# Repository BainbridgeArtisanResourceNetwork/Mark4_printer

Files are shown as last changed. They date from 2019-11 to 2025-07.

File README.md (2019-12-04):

# Mark4_printer
Mark4 is the large-format 3D printer the ETA studio at BARN is building as a DIY community project.

## Specifications

- Motion stage: CoreXY
- Build volume: X=350mm, Y=350mm, Z>=400mm
- Controller: Duet 2 WiFi
- Extruder/Hot-end: Bondtech BMG-M & Mosquito 

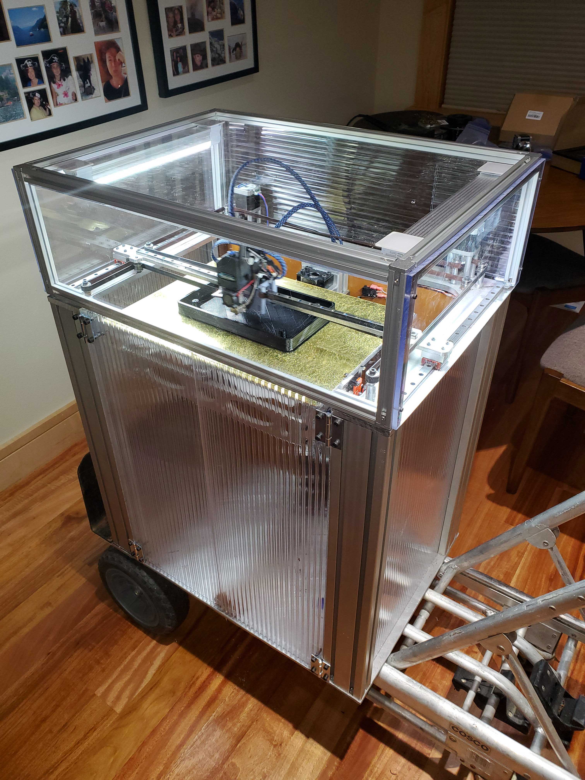
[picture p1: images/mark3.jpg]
Mark3


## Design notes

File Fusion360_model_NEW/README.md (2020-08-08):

### The Mark4 Fusion 360 model

**2020-01-30 Current state of the model**

New Assembly  (file: Mark4 Assembly v231.f3d)
Assembly, Mark4 printer v231

 Changes from last version (Mark4 Assembly v134.f3d):

- Moved pulleys on bridge by 0.2mm to align with Jubilee carriage backplate V 05. Part of github issue #24.
- Changed X-Rail block to MGN12C from MGN 12H. 
- Replaced older versions of Jubilee carriage parts with latest versions.
- Implemented changes to some bugs reported in github
  - #21 - changed heated bed dimensions to match 350mm x350mm goal of project.
  - #20 - X-axis motor mount screw holes too big.
  - #18 - Mounting holes for kinematic bed attach do not line up with posts on the supports
- Removed prototype belt tensioners that didn't work in the wood proto.
- Added electronics and proto board for supporting same.

**Next steps with the model:**

- Detail the bottom and top enclosures.
- Add details driven by the electronics (locations for the Power supply, boards, user interface, limit switch mounting, etc.)
- Tweak the Jubilee tool changer dock so it mounts to our printer.
- Play with the cable/filament  bundles to see how they should impact the design of the top cover.

**About the stuff in this directory (updated since 2020-01-07):**

This directory of the repo contains the "master" versions of the BARN Mark4 printer.  Ideally, you'll only find the series of model versions, this readme.md file, and a folder for images used in this readme. 

We are trying to accommodate Fusion360 users with Personal licenses, which means that we cannot have a shared project in Fusion360. As a result we are using the following process to create the assembly file here. You can create your own assembly file using this process or upload ours into your own Fusion 360 project.

Our Fusion 360 process (updated 1/7/2020):

1. The master assembly for the Mark 4 project is in one member's (Mike's at present) Fusion account.  This person is called the master librarian.

2. Parts in the project are added to the Mark4 master assembly.

3. The resulting assembly file is Exported and put into this directory.

4. Design collaboration is achieved my other users uploading the file to their Fusion 360 account and working on it there. When collaborative changes are to be added to the master we'll do one of the following:

     A. New parts - The collaborator provides a copy of their modified assembly (maybe/probably in github?). New parts will be copied (inlinked) from the collaborator design into the master, and the master updated.

     B. Edits of existing parts -  The master librarian will replicate the changes into the master mode, or replace the existing master model with the collaborators.

   Let's all agree that this is a far from perfect method for collaboration.  

A note from the master librarian (currently Mike) : I am building the assembly "outward" from the print head. This means starting with the Xrail and adding a print head on it. , then restricting the motion of this to our target 350mm (plus some space for an offset second extruder). This is then added to the Y rails and similarly motion restricted (adding space for a future tool changer). After this we can add the CoreXY belts, pullies, motors, etc. and also a frame subassembly.

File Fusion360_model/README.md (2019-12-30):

### The Mark4 Fusion 360 model

**2019-12-30 Current state of the model**

New Assembly V15:
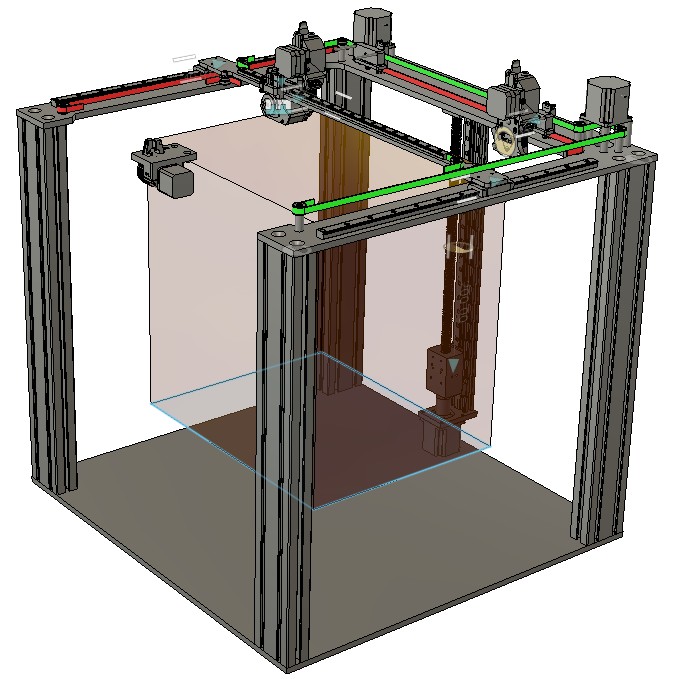
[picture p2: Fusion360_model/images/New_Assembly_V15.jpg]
Assembly, Mark4 printer v23


- Added the Jubilee tool changer as a "volume placeholder" so that we can assess the impact/value of toolchangers with a better model than I could find for the E3D changer.  
  		
  * The Jubilee has a single nozzle extruder (not mosquito) and a Bondtech extruder. 
  * Both the old extruder and the Jubilee are in the model. If you turn them both on, you'll be really confused!
  * There is a part floating in the front of the frame. This houses the Jubilee's tool-changing motor, which uses a cable to latch and unlatch the tools during a tool-change.  
  * I put in the Jubilee as-is, but we'd need to make changes if we want to pursue it. The jubilee X-rail is mounted to the bottom of the bridge, and the tool docks as-imported and placed interfere with the belts at the back of the frame. 

**Next steps with the model:**

- Make some decisions about a tool changer - do we have one, and if so, which one? I'm personally leaning towards having one, even if we only change tools by hand. It's a handy way to easily swap tools. 
- Add the build plate support and build plate.

This will complete the "basic" design, then there are several things for us to look at before locking things in:

- Assessing a three-rail (and motor) Z-axis vs a single rail, cantilevered design. 
- After these are done, we can  add both the main enclosure and the top enclosure, electronics, etc..

**About the stuff in this directory (unchanged since 2019-12-11):**

This directory of the repo contains the "master" versions of the parts we are assembling into the BARN Mark4 printer. It also contains a Fusion 360 assembly of many (most, probably not all) of these parts.

We are trying to accommodate Fusion360 users with Personal licenses, which means that we cannot have a shared project in Fusion360. As a result we are using the following process to create the assembly file here. You can create your own assembly file using this process or upload ours into your own Fusion 360 project.

Our Fusion 360 process (updated 12/11/2019):

1. Individual part designs (or subassemblies, in some cases) are added to the Mark 4 project in one members (Mike's at present) Fusion account.  
2. Parts in the project are added to the Mark4 master assembly.
3. The resulting assembly file is Exported and put into this directory.

It's (still) a bit of a clumsy process, but anyone can upload the assembly into a project in their own Fusion account and the latest version of all the parts are added to the project too.  

A note from the assembler (currently Mike) : I am building the assembly "outward" from the print head. This means starting with the Xrail and adding a print head on it. , then restricting the motion of this to our target 350mm (plus some space for an offset second extruder). This is then added to the Y rails and similarly motion restricted (adding space for a future tool changer). After this we can add the CoreXY belts, pullies, motors, etc. and also a frame subassembly.

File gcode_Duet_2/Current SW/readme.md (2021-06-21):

# BARN Mark4 Printer SW

This folder contains the latest "released" software for the BARN Mark 4 printer.  By "software", we mean the gcode files we've created/evolved from other sources, and the web software provided with the Duet2 controller board. We have not made any changes to the web software, so this means that for us, "software" means the gcode files.

gcode files are used for all interfacing to the Duet2 firmware in the BARN printer. It's used for parts that are being printed, but also for initializing the Duet2 hardware with the specific parameters of our machine, the methods for homing at startup, the methods for changing filaments, and the instructions for changing tools.  A couple of gcode references we used a **lot** are the [Duet3d wiki](https://duet3d.dozuki.com/Wiki/Gcode?revisionid=HEAD) and [RepRap gcode wiki](https://reprap.org/wiki/G-code)

This directory organization and the file names within are mostly as provided by Duet3d (the company that makes the Duet2 controller board). We will strive to put lots of comments into the files as we modify  and/or create them, so reading the files is a way to learn what we are doing. We are also using a short phython script to extract certain comments from the gcode files into MD files as a way to provide the new reader an overview of what the gcode in the file is doing.  So, for every .gcode file, there is a companion .md file.

## Use of this sw

To put this software on the BARN printer, the whole contents of the directory and all it's sub-directories are copied onto a microSD card and the card inserted into the SD slot on the Duet2 controller board on the printer. At power up, the controller looks on the SD, finds the files it needs, and gets going.

## Directories

The following directories are part of the  software. Their use is briefly described here. Additional info can be found on the Duet2 wiki [HERE](https://duet3d.dozuki.com/Wiki/Firmware_Overview).  Each of these directories should contain a readme.md that describes it's files and their use.

### filaments

This file has folders for different filament types and those directories have gcode that is executed when a filament load or unload command is given. They have stuff like heating the nozzle before extracting the filament, running the extruder in reverse to pull the filament out of the nozzle, etc.  This folder does not appear to have been created by Duet2, but is inherited from Jubilee (a theory). We'll need to dig into it's use.

### gcodes

Folder **/gcodes** is used to hold g-code files for  printing. You can use subfolders of /gcodes to organize these files.  G-code files can also be located on an external SD card if one is  connected.  Files in this directory can be executed from the Duet2 web interface or touchscreen,

### macros

Folder **/macros** is used to hold used-defined macro  files. "Macros" are really just gcode files that are usually called macros if they are used by another gcode file.  The names of these files appear as menu entries in DuetWebControl and on PanelDue.  You can use subfolders of /macros to organize these  files.  Macros created by BARN members are named starting with "BARN_". Files in this directory can be executed from the Duet2 web interface or touchscreen.

### sys

This directory contains the gcode files used for initializing the Duet2 board. It's the place to start if you're looking for something. 

### www

This directory contains some html, css, and other files that the Duet 2 uses for things we don't yet understand. Maybe it's the web interface for the Duet2, or maybe something else. The Duet controller apparently also copies the contents of the filaments, gcodes, macros, and sys folders  into this directory.

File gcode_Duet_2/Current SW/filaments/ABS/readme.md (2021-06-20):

# filaments\ABS directory
This directory contains gcode macros (files) that are executed when ABS filament is selected to be loaded or unloaded. 

The gcode files in this directory and the sumamries from their comments (if available) are listed below.

### load.g
This file contains the steps that the machine will take when there is a load request for ABS filament.  It includes messages to be displayed to the user ("Wait for the nozzle to heat before inserting the filament", etc.). If the extruder is a bowden style, this is where the commands for shooting the filament through the tube to the hot end will be. We probably need to figure out how to make a file that is both filament and tool specific. Differnet tools may have different load/unload requirements. And this maccro does not care if the tool is docked ot undocked.

### unload.g
This file contains the steps that the machine will take when there is an unload request for PLA filament.  It includes messages to be displayed to the user ("Wait for the nozzle to heat", etc.). If the extruder is a bowden style, this is where the commands for pulling the filament back through the tube to the extruder will be. We probably need to figure out how to make a file that is both filament and tool specific. Differnet tools may have different load/unload requirements. And this maccro does not care if the tool is docked ot undocked.

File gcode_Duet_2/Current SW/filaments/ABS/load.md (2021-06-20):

*this is an auto-generated md file for the **filaments\ABS\load.g**  *gcode file. All comments in the original file with a '!' immediately following the ';' are collected here.*
<summary>This file contains the steps that the machine will take when there is a load request for ABS filament.  It includes messages to be displayed to the user ("Wait for the nozzle to heat before inserting the filament", etc.). If the extruder is a bowden style, this is where the commands for shooting the filament through the tube to the hot end will be. We probably need to figure out how to make a file that is both filament and tool specific. Differnet tools may have different load/unload requirements. And this maccro does not care if the tool is docked ot undocked.
 Display a message for the user to wait for nozzle heating
Heat the nozzle - we should replace G10 with M658. G10 is being deprecated.
Wait for the temperature to reach it's set point. We need to add a P to to this M116 to make it tool specific.
The extruder is hot, execute a sequence of commands to load the filament. 
 looks like this file was created for a bowden tube.
 Feed 10mm of filament at 600mm/min.  Initial grab of the filament by the extruder
 Feed 470mm of filament at 3000mm/min. Quickly Feed filament all the way to the hot end.
 Feed 20mm of filament at 300mm/min. Slowly feed filament into the hot end
 Retract 10mm of filament at 1800mm/min to releieve pressure in the hot end and forestall oozing.
 Turn off the heater again. Filament is loaded.

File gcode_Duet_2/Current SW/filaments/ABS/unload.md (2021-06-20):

*this is an auto-generated md file for the **filaments\ABS\unload.g**  *gcode file. All comments in the original file with a '!' immediately following the ';' are collected here.*
<summary>This file contains the steps that the machine will take when there is an unload request for PLA filament.  It includes messages to be displayed to the user ("Wait for the nozzle to heat", etc.). If the extruder is a bowden style, this is where the commands for pulling the filament back through the tube to the extruder will be. We probably need to figure out how to make a file that is both filament and tool specific. Differnet tools may have different load/unload requirements. And this maccro does not care if the tool is docked ot undocked.
 Display a message for the user to wait for nozzle heating
Heat the nozzle - we should replace G10 with M658. G10 is being deprecated.
Wait for the temperature to reach it's set point. We need to add a P to to this M116 to make it tool specific.
The extruder is hot, execute a sequence of commands to load the filament.
 Retract 20mm of filament at 300mm/min. slowly pull the filament out of the hot end.
 Retract 480mm of filament at 3000mm/min Quickly pull the filament out of the bowden tube

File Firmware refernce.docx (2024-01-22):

| Bed | Tool 0 | Tool 1
Heaters Number Duet plug | 0 | ~~2~~ 1 ~~e1heat~~ e0heat | ~~1~~ 2 ~~e0heat~~ e1heat
Sensor Number (temperature) Duet plug | 0 bedtemp | ~~2~~ 1 ~~e1temp~~ e0temp | ~~1~~ 2 ~~e0temp~~ e1temp
Extruder driver Number Duet plug | | ~~4~~ 3 ~~E1 motor~~ E0 Motor | ~~3~~ 4 ~~E0 Motor~~ E1 motor
Fans Number (hot end) Duet plug | | ~~3~~ 0 ~~duex.fan3~~ fan0 | ~~0~~ 2 ~~fan0~~ duex.fan3
Fans Number (Part) Duet plug | | ~~4~~ 1 ~~duex.fan4~~ fan2 | ~~2~~ 3 ~~fan 2~~ duex.fan4

Full motor/driver table

Use | Driver Number | Duet/duex connection
X motor | 0 | X
Y motor | 1 | Y
| 2
Tool #0 Extruder | ~~4~~ 3 | ~~E1 motor~~ E0 motor
Tool #1 Extruder | ~~3~~ 4 | ~~E0 motor~~ E1 motor
Z motor (Front-left) | 6 | duex E3
Z motor (Front-right) | 7 | duex E4
Z motor (Rear) | 8 | duex E5

Full Fan Table

Use | Fan Number | Duet/duex connection
Tool 0 hot end fan | ~~3~~ 0 | ~~duex.fan3~~ fan 0
Tool 0 Part cooling fan | ~~4~~ 1 | ~~duex.fan4~~ fan 1
Tool 1 Hot end fan | ~~0~~ 2 | ~~Fan 0~~ duex.fan3
Tool 1 Part cooling fan | ~~2~~ 2 | ~~fan 2~~ duex.fan4

Full Heater Table

Use | Heater Number | Duet/duex connection
Bed heater | 0 | bedheat
Tool 0 / Extruder 0 | 1 | e0heat
Tool 1 / Extruder 1 | 2 | e1heat

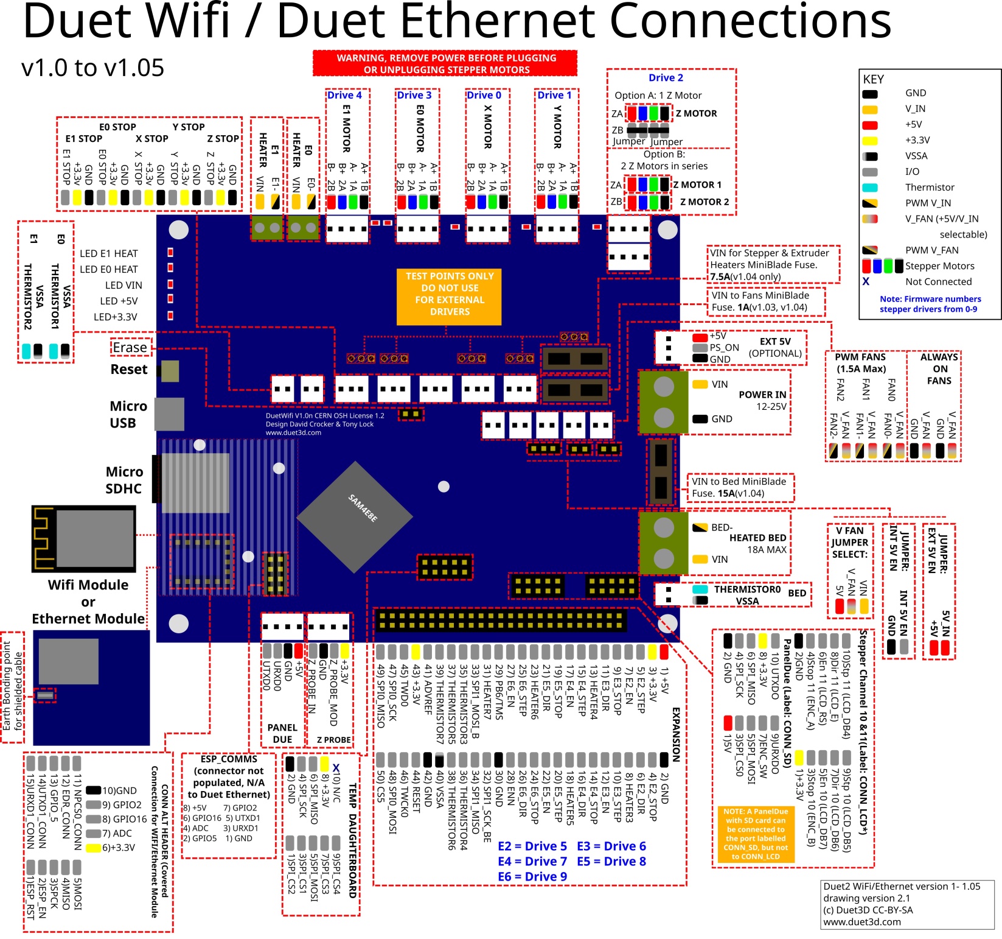
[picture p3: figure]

Duet2 Pin names

In the table below, multiple names on a line are aliases for a single pin. Some pins (primarily heater pins) have an inversion between the processor and the corresponding output, RRF3 will automatically allow for this inversion. These pins are marked with a * after the pin name in the list below. For legacy reasons some Duex pins are inverted or not, depending on the name/alias used to access them. This is indicated with a ! in front of the pin name in the sable below. e.g. exp.heater3 is the same pin as !duex.e2heat the ! indicates that the logic of the pin is inverted when referred to as "duex.e2heat"

Pin label on Duet PCB/wiring diagram | RRF3 Pin name (Duet) | Notes / Shared with (on Duex/BoB)
Heater outputs
BED HEAT | bedheat *
E0 HEAT | e0heat *
E1 HEAT | e1heat *
EXPANSION HEADER HEATER3 (pin 8) | exp.heater3, exp.8 | !duex.e2heat, !duex.pwm1
EXPANSION HEADER HEATER4 (pin 13) | exp.heater4, exp.13 | !duex.e3heat, !duex.pwm2
EXPANSION HEADER HEATER5 (pin 18) | exp.heater5, exp.18 | !duex.e4heat, !duex.pwm3
EXPANSION HEADER HEATER6 (pin 23) | exp.heater6, exp.23 | !duex.e5heat, !duex.pwm4
EXPANSION HEADER HEATER7 (pin 31) | exp.heater7, exp.31 | !duex.e6heat, !duex.pwm5
Temperature inputs
BED TEMP | bedtemp
E0 TEMP | e0temp
E1 TEMP | e1temp
EXPANSION HEADER THERM3 (pin 35) | e2temp, exp.thermistor3, exp.35 | duex.e2temp
EXPANSION HEADER THERM4 (pin 36) | e3temp, exp.thermistor4, exp.36 | duex.e3temp
EXPANSION HEADER THERM5 (pin 37) | e4temp, exp.thermistor5, exp.37 | duex.e4temp
EXPANSION HEADER THERM6 (pin 38) | e5temp, exp.thermistor6, exp.38 | duex.e5temp
EXPANSION HEADER THERM7 (pin 39) | e6temp, exp.thermistor7, exp.39 | duex.e6temp
Fan outputs
FAN0 | fan0
FAN1 | fan1
FAN2 | fan2
Endstop inputs
X_STOP | xstop
Y_STOP | ystop
Z_STOP | zstop
E0_STOP | e0stop
E1_STOP | e1stop
EXPANSION HEADER E2_STOP (pin 4) | exp.e2stop, exp.4
EXPANSION HEADER E3_STOP (pin 9) | exp.e3stop, exp.9 | duex.cs6
EXPANSION HEADER E4_STOP (pin 14) | exp.e4stop, exp.14 | duex.cs7
EXPANSION HEADER E5_STOP (pin 19) | exp.e5stop, exp.19 | duex.cs8
EXPANSION HEADER E6_STOP (pin 24) | exp.e6stop, exp.24
Miscellaneous
Probe IN | zprobe.in
Probe MOD | zprobe.mod
CONN_LCD ENC_B | connlcd.encb, connlcd.3 | (also used for endstop 11)
CONN_LCD ENC_A | connlcd.enca, connlcd.4 | (also used for endstop 10)
CONN_SD ENC_SW | connsd.encsw, connsd.7
EXPANSION HEADER PB6/TMS (pin 29) | exp.pb6, exp.29 | duex.pb6
SPI CS
SPIO CS1 (Temp DB, pin 3) | spi.cs1
SPIO CS2 (Temp DB, pin 1) | spi.cs2
SPIO CS3 (Temp DB, pin 7) | spi.cs3
SPIO CS4 (Temp DB, pin 9) | spi.cs4
EXPANSION HEADER CS5 (pin 50) | spi.cs5, exp.50 | duex.cs5
EXPANSION HEADER E3_STOP (pin 9) | spi.cs6, exp.e3stop, exp.9 | duex.cs6
EXPANSION HEADER E4_STOP (pin 14) | spi.cs7, exp.e4stop, exp.14 | duex.cs7
EXPANSION HEADER E5_STOP (pin 19) | spi.cs8, exp.e5stop, exp.19 | duex.cs8

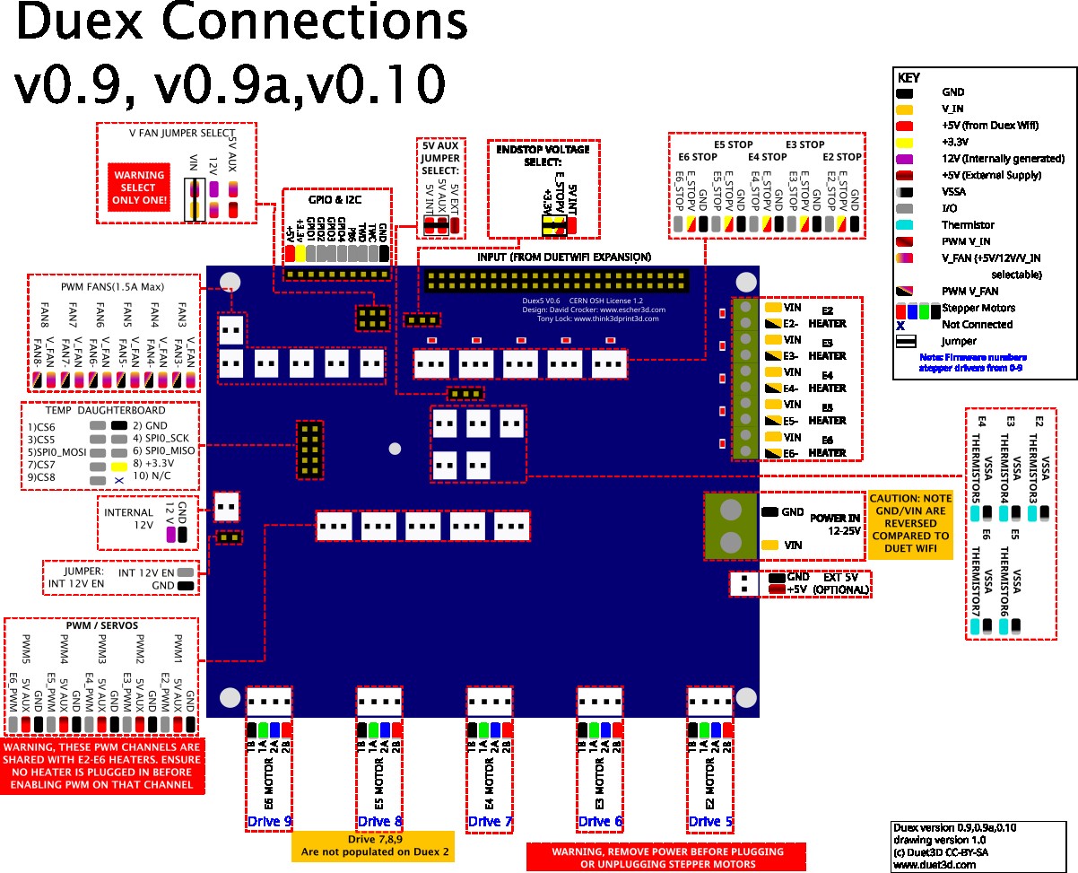
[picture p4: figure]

Label/pin on DueX PCB/wiring diagram | RRF3 Pin name (DueX) | Shared with (on Duet)
Heater outputs
E2 HEATER, E2-, PWM_1, E2_PWM | duex.e2heat, duex.pwm1 | !exp.heater3, !exp.8
E3 HEATER, E3-, PWM_2, E3_PWM | duex.e3heat, duex.pwm2 | !exp.heater4, !exp.13
E4 HEATER, E4-, PWM_3, E4_PWM | duex.e4heat, duex.pwm3 | !exp.heater5, !exp.18
E5 HEATER, E5-, PWM_4, E5_PWM | duex.e5heat, duex.pwm4 | !exp.heater6, !exp.23
E6 HEATER, E6-, PWM_5, E6_PWM | duex.e6heat, duex.pwm5 | !exp.heater7, !exp.31
Temperature inputs
E2_THERMSTOR3 | duex.e2temp | e2temp, exp.thermistor3, exp.35
E3_THERMSTOR4 | duex.e3temp | e3temp, exp.thermistor4, exp.36
E4_THERMSTOR5 | duex.e4temp | e4temp, exp.thermistor5, exp.37
E5_THERMSTOR6 | duex.e5temp | e5temp, exp.thermistor6, exp.38
E6_THERMSTOR7 | duex.e6temp | e6temp, exp.thermistor7, exp.39
Fan outputs
FAN3 FAN3- | duex.fan3 | Note: the duex.fan pins cannot be used to control a laser.
FAN4 FAN4- | duex.fan4
FAN5 FAN5- | duex.fan5
FAN6 FAN6- | duex.fan6
FAN7 FAN7- | duex.fan7
FAN8 FAN8- | duex.fan8
Endstop inputs
E2_STOP | duex.e2stop | The duex.estop pins are routed through the I2C expander on the DueX. The exp.e[x]stop pins on the Duet expansion header become the CS pins on the DueX temp daughterboard connector.
E3_STOP | duex.e3stop
E4_STOP | duex.e4stop
E5_STOP | duex.e5stop
E6_STOP | duex.e6stop
Miscellaneous
GPIO & I2C PB6 | duex.pb6 | exp.pb6, exp.29
GPIO & I2C GPIO1 | duex.gp1 | Note: the duex.gp1-4 pins cannot be used to control a laser.
GPIO & I2C GPIO2 | duex.gp2 | Note: the duex.gp1-4 pins have a permanent 10K pullup to 5V
GPIO & I2C GPIO3 | duex.gp3
GPIO & I2C GPIO4 | duex.gp4
SPI CS
TEMP DB CS5 | duex.cs5 | spi.cs5, exp.50
TEMP DB CS6 | duex.cs6 | spi.cs6, exp.e3stop, exp.9
TEMP DB CS7 | duex.cs7 | spi.cs7, exp.e4stop, exp.14
TEMP DB CS8 | duex.cs8 | spi.cs8, exp.e5stop, exp.19

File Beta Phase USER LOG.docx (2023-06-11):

USER LOG - BETA

TechLab Large 3D Printer – Mark4

During the Beta phase of the printer, users should log all print jobs that they start.

Date | User name | Filament type

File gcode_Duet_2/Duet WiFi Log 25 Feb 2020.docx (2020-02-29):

2/25/2020 BARN Large 3D Printer Electrical Log

1. Energized the Duet WiFi control board via the Power In 12-24 V terminals from the Eagwell 24VDC, 360 Watt power supply, to verify operability and to check board input current via the inline wattmeter I installed. Found load current to be around 110 mAmps. At 24.2 VDC. De-energized the Eagwell power supply and disconnected the 24VDC from the board to prepare to test the board’s USB interface, note that the USB interconnect is not to be concurrently installed with external DC power applied to the board’s 12-24 V terminals.
2. Loaded YAT terminal control program on my PC and connected a micro USB to USB cable between the Duet WiFi board and an USB port on my PC. YAT was unable to connect to the board via the USB interface, even though the Blue onboard USB LED was illuminated. At this point, a different USB-to-micro USB cable was installed with no change. The supplied and installed micro SD card was then removed and at that time, YAT was able to connect with no card inserted on COM3. The removed micro SD card was then installed in an SD card carrier and inserted into the PC SD card slot and was found to be unreadable. A different micro SD card was then acquired and formatted, but not installed. An M115 command was then sent via YAT to the board to determine its firmware version, which was reported back as:

Firmware Version: 2.0 (RTOS)

Duet WiFi: 1.02

Firmware Date: 2018-06-05b3

3. The Duet “Installing and Updating Firmware” page: (https://duet3d.dozuki.com/Wiki/Installing_and_Updating_Firmware)

was then consulted to identify the latest firmware versions for our Duet WiFi board. Based upon this, the latest version was found to be release 2.05.1 (Duet2), 1,26.1 (Duet 06/085). The micro SD card to be installed in the Duet board’s micro SD card slot is required to have a specific file configuration for /sys and /www files. The /sys file config on the SD card is as follows:

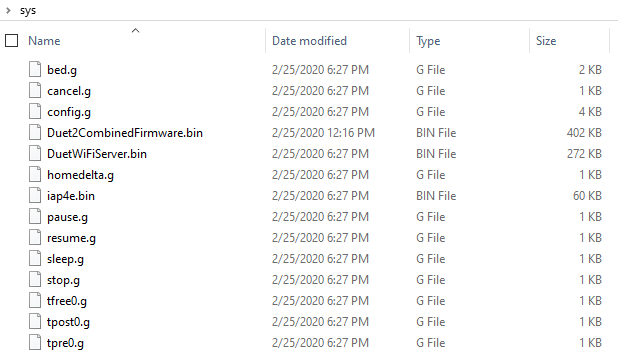
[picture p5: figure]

The /www file configuration on the SD card is as follows:

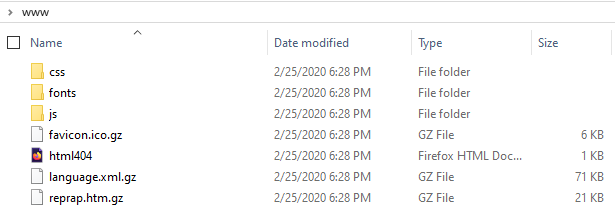
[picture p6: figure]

It should be noted that the file DuetWiFiServer.bin was renamed from its downloaded file name DuetWiFiServer-1.23.bin as directed: “They must have exactly those filenames, so if the files you downloaded had the version number included in the filename, then you will need to rename them”. The configured SD card was then installed in the Duet WiFi slot.

4. At this point, the YAT terminal was used to send the Install Main Firmware command: M997 S0 which then installed the main firmware. Then, the YAT terminal was used to send the Install WiFi Module Firmware command: M997 S1 which then installed the WiFi Module firmware. To verify that these firmware upgrades were indeed installed, YAT terminal was used to send the Firmware Version Query command: M115, giving the following reply:

FIRMWARE_NAME: RepRapFirmware for Duet 2 WiFi/Ethernet FIRMWARE_VERSION: 2.05.1 ELECTRONICS: Duet WiFi 1.02 or later FIRMWARE_DATE: 2020-02-09b1<LF>ok<LF>

The YAT terminal was then used to send the WiFi Firmware Version query command: M122 giving the following reply:

=== Diagnostics ===<LF>RepRapFirmware for Duet 2 WiFi/Ethernet version 2.05.1 running on Duet WiFi 1.02 or later<LF>Board ID: 08DJM-9178L-L4MSJ-6JKD4-3SN6T-1T1YQ<LF>Used output buffers: 1 of 24 (1 max)<LF>=== RTOS ===<LF>Static ram: 25712<LF>Dynamic ram: 92836 of which 164 recycled<LF>Exception stack ram used: 312<LF>Never used ram: 12048<LF>Tasks: NETWORK(ready,1448) HEAT(blocked,912) MAIN(running,3816) IDLE(ready,160)<LF>Owned mutexes:<LF>=== Platform ===<LF>Last reset 03:16:20 ago, cause: power up<LF>Last software reset at 2019-11-23 20:35, reason: User, spinning module GCodes, available RAM 6404 bytes (slot 1)<LF>Software reset code 0x0003 HFSR 0x00000000 CFSR 0x00000000 ICSR 0x0041f000 BFAR 0xe000ed38 SP 0xffffffff Task 0xffffffff<LF>Error status: 0<LF>Free file entries: 10<LF>SD card 0 detected, interface speed: 20.0MBytes/sec<LF>SD card longest block write time: 0.0ms, max retries 0<LF>MCU temperature: min 16.3, current 25.0, max 27.1<LF>Supply voltage: min 1.5, current 1.7, max 1.7, under voltage events: 0, over voltage events: 0, power [Warning: Maximal number of bytes per line exceeded! Check the EOL (end-of-line) settings or increase the limit in the advanced terminal settings.]

5. At this point, the YAT terminal was used to send the Add WiFi host network to remembered list command: M587 S"ccc" Network SSID P"ccc" Network password, adding the identified host network. The YAT terminal was then used to send the Set IP address, enable/disable network interface command: M552 S1 which illuminated the BLUE wireless LED and connected the Duet to the host network. The below image details the Duet WiFi board at this point, the left-most GREEN LED indicating available 5 VDC, the right-most GREEN LED indicating 3.3 VDC available, the left-most BLUE LED indicating USB connected and the right-most BLUE LED indicating WiFi activated.

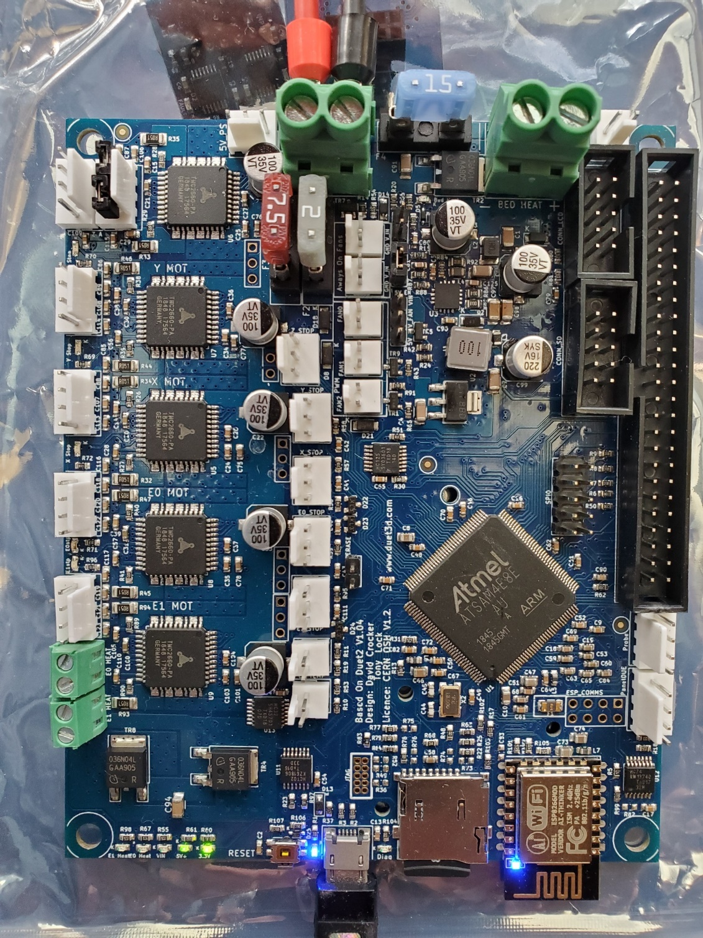
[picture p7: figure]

Duet WiFi Board Energized VIA USB

6. Referencing the Duet Wiki: https://duet3d.dozuki.com/Wiki/Gcode, the following M commands were used VIA YAT to command the Duet WiFi board:

M115: Get Firmware Version and Capabilities

Parameters

- This command can be used without any additional parameters.
- Pnnn Electronics type (See Notes)
- Bnnn Board number (RRF_3/Duet 3 only, see Notes)

Examples

- M115
- M115 P2

Request the Firmware Version and Capabilities of the current microcontroller.

The details are returned to the host computer as key:value pairs separated by spaces and terminated with a linefeed.:

M115

FIRMWARE_NAME: RepRapFirmware for Duet 2 WiFi/Ethernet FIRMWARE_VERSION: 2.04RC1 ELECTRONICS: Duet WiFi 1.0 or 1.01 FIRMWARE_DATE: 2019-07-14b1

See the M408 command for a more comprehensive report on machine capabilities.

Notes

The 'P' parameter is used tell the firmware about the hardware on which it is running, if RRF can't identify it. Should only be used in config.g, if you're having problems. If the P parameter is present then the integer argument specifies the hardware being used. The following are supported on first-generation Duets:

- M115 P0 - Automatic board type selection if supported, or default if not
- M115 P1 - Duet 0.6
- M115 P2 - Duet 0.7
- M115 P3 - Duet 0.85

The 'B' parameter is used on Duet 3 only, using RRF_3. M115 can take an optional B (board number) parameter which is the CAN address of the board to be queried, default 0 (i.e. main board). Example:

M115 B1

Board EXP3HC firmware 3.0beta1 2019-10-28b1

M122: Diagnose

Parameters

- This command can be used without any additional parameters.
- Pnnn report specific information (See Notes)
- Bnnn Board number (RRF_3/Duet 3 only, see Notes)
- "DSF" Immediate DSF diagnostics (RRF_3/Duet3 only with attached SBC)

Example

- M122

Sending an M122 causes the RepRap to transmit diagnostic information.

Notes

The 'P' parameter is used to report specific information. The details vary between releases. As at RepRapFirmware version 2.03 they are:

- P1 print summary test report (additional parameters: Taa:bb = min/max accepted MCU temperature reading, Vaa:bb = min/max VIN voltage reading, Waa:bb = min/max 12V regulator voltage reading if applicable)
- P100 print a summary of recent moves (only if move logging is enabled in the firmware build)
- P101 print the status of an attached DueX expansion board
- P102 print how long it takes to evaluate the square root of a 62-bit unsigned integer
- P103 print how long it takes to evaluate sine and cosine
- P104 print how long it takes to write a file to the SD card (specify the file size in Mbytes in the S parameter, default 10)
- P105 print the sizes of various objects used by RepRapFirmware

Note: do not use M122 with a P parameter of 1000 or greater. There are a few values that deliberately cause the firmware to crash, which are used to test the error reporting facilities. As at firmware 2.03 these are:

- P1001 cause a watchdog reset
- P1002 test what happens when a module gets stuck in a spin loop
- P1003 test what happens when we write a blocking message to USB
- P1004 test integer division by zero
- P1005 test the response to an unaligned memory access
- P1006 test the response to accessing an invalid region of memory

The 'B' parameter is used in RepRapFirmware 3 on Duet 3 only, to report diagnostic information from connected boards. The B (board number) parameter is the CAN address of the board to be queried, default 0 (i.e. main board). Example:

M122 B1

Diagnostics for board 1:

Board EXP3HC firmware 3.0beta1 2019-10-28b1

Never used RAM 163.4Kb, max stack 376b

HEAT 1284 CanAsync 1456 CanRecv 1424 TMC 168 AIN 532 MAIN 2220

Driver 0: standstill, reads 26609, writes 11 timeouts 0, SG min/max 0/0

Driver 1: standstill, reads 26611, writes 11 timeouts 0, SG min/max 0/0

Driver 2: standstill, reads 26614, writes 11 timeouts 0, SG min/max 0/0

Move hiccups: 0

VIN: 24.4V, V12: 12.2V

MCU temperature: min 43.8C, current 43.9C, max 44.1C

M552: Set IP address, enable/disable network interface

Parameters for Duet 2 Ethernet and 06/085

- Pnnn IP address, 0.0.0.0 means acquire an IP address using DHCP
- Snnn 0 = disable networking, 1 = enable networking
- Rnnn (optional, RepRapFirmware 1.17 and earlier only) HTTP port, default 80 Parameters for Duet 2 WiFi
- P"ssid" (optional, RepRapFirmware 1.20 and later) SSID of network to connect to. The SSID and password must already have been registered using M587. If this parameter is not present, the Duet 2 WiFi will try to connect to the strongest network that is broadcasting its SSID and whose SSID has been registered using M587.
- Snnn 0 = disable networking, 1 = enable networking as a client, 2 = enable networking as an access point , -1 = disable WiFi module

Example (Duet 2 Ethernet)

- M552 S1 P192.168.1.14

Sets the IP address of the machine to (in this case) 192.168.1.14. If the S parameter is not present then the enable/disable state of the network interface is not changed.

Example (Duet 2 WiFi)

- M552 S1 P"MyNetwork"

M552 with no parameters reports the current network state and IP address.

In firmware 1.18 and later the HTTP port address is set using the M586 command, so the R parameter of this command is no longer supported.

On the Duet 2 WiFi running firmware 1.19 and later, the IP address is set in the M587 command when you configure the access point details.

M587: Add WiFi host network to remembered list, or list remembered networks

This command must not be used in the config.g file

Parameters:

- S"ccc" Network SSID
- P"ccc" Network password
- Inn.nn.nn.nn (optional) IP address to use when connected to this network. If zero or not specified then an IP address will be acquired via DHCP.
- Jnn.nn.nn.nn (optional) Gateway IP address to use when connected to this network.
- Knn.nn.nn.nn (optional) Netmask to use when connected to this network

The SSID and password must always be enclosed in double quotation marks.

Notes

Many programs used to send GCodes convert all characters to uppercase. In firmware 1.19.2 and later, within any quoted string you can use a single-quote character to indicate that the following character should be changed to lowercase. For example, M587 S"ABC" P"P'A'S'SW'O'R'D" would specify that the password is "PassWord". Use two single quote characters to represent one actual single quote character in the password or in the SSID. For example, if your SSID is "Pete's network" then enter "Pete''s network".

M587 with no parameters lists all the remembered SSIDs, but not the remembered passwords.

The M587 command will fail if the WiFi module has not yet been taken out of reset. So if the WiFi module has not been started, send M552 S0 to put it in idle mode first.

Important! Do not use M587 within config.g. As well as being a security hazard, writing the access point parameters to WiFi chip every time you start the Duet may eventually wear out the flash memory. Also, the wifi module does not get enabled until the end of running config.g. It is better to use a macro to send M587 (source: https://forum.duet3d.com/post/42798)

M588: Forget WiFi host network

This command must not be used in the config,g file

Parameters:

- S"ccc" Network SSID to remove from the remembered list

The specified SSID will be removed from the remembered list and the associated password cleared out of EEPROM. If the SSID is given as "*" then all remembered networks will be forgotten.

The M588 command will fail if the WiFi module has not yet been taken out of reset. So if the WiFi module has not been started, send M552 S0 to put it in idle mode first. M588 does not work from within config.g at startup.

M997: Perform in-application firmware update

Parameters

- Snnn Firmware module number(s), default 0
- Bnnn CAN address of the board to be updated (RRF_3, Duet 3 only)

Example:

- M997 S0:1 - update firmware modules 0 and 1

Notes

This command triggers a firmware update if the necessary files are present on the SD card. In RepRapFirmware on the Duet series, module numbers are as follows:

- 0 - main firmware, filename sys/RepRapFirmware.bin (older Duets) or sys/Duet2CombinedFirmware (Duet 2). File sys/iap.bin (Duet) or sys/iap4e.bin (Duet 2) must also be present.
- 1 - web server firmware, filename sys/DuetWiFiServer.bin (Duet 2 WiFi only)
- 2 - web server file system, filename sys/DuetWebControl.bin (needed only when using RepRapFirmware 1.18 series and earlier for Duet 2 WiFi)
- 3 - put the WiFi module into bootloader mode, so that firmware can be uploaded directly via its serial port

On Duet 3 only this command take an optional B (board number) parameter which is the CAN address of the board to be updated, default 0 (i.e. main board).

See Installing and Updating Firmware (https://duet3d.dozuki.com/Wiki/Installing_and_Updating_Firmware) for detailed documentation.

This ends todays efforts

REM

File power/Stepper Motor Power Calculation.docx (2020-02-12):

STEPPER MOTOR LOAD CALCS AND TYPES

Typical bipolar stepper data sheets define amps/phase, phase resistance, rated voltage, phase inductance, holding torque and step angle (see below). Calculations to determine actual power supply power loads when driven by a motor driver IC (e.g. Trinamic TMC2209) for two phase steppers are not intuitive. The Duet guidelines for determining power supply sizing when utilizing their Duet 2 WiFi V1.04 control board are as follows:

Stepper motors: at full rated current, the power needed for each motor is its rated current times its rated voltage (if no rated voltage is specified, use the square of the rated current times the phase resistance). This is the power at standstill. To allow for driver losses and the extra power needed to create acceleration, add 50%. Multiply by the number of stepper motors.

In an observed test of 5 NEMA 17 0.9 deg steppers (specific model not known) connected to a Duet-like control board with a 24 VDC power supply, the total DC current supplied to the drivers during varied concurrent actuations was not observed to exceed approximately 1 amp, even with applied loads. Based upon this result, the power required by the 5 NEMA 17 stepper motors from the 24 VDC power supply in this instance would be approximately 24 watts or 4.8 watts per stepper motor.

Since the specific phase current, phase resistance or phase voltage were not known for the observed test detailed above, the values for the planned BARN large printer NEMA 17 steppers will be utilized to attempt to verify the Duet-suggested guidelines for power supply sizing. The NEMA 17 stepper motors selected for the “Z” axis: OSM Technology, P/N 17HM19-1684S, have a phase current of 1.68 DC amps, phase resistance of 1.65 ohms, phase voltage of 2.8 VDC, phase inductance of 4.1 mH and a holding torque of 0.42 Nm.

DUET Suggested Stepper Power Calculation Method #1

If the Duet-suggested power supply sizing guidelines for stepper motors are applied, the following power consumption estimate per stepper is found:

Psp = (Iph)²*Rph

NEMA 17 Motor

Psp = Stepper Power

Iph= Rated Phase Current 1.68 Amps

Rph = Phase Resistance 1.65 Ohms

Psp = (1.68)²*1.65 = 4.66 Watts

This is close to the results from the observed test, where individual stepper power was observed to be approximately 4.8 watts.

If the suggested 50%for driver losses and the extra power needed to create acceleration is added, stepper power is estimated at 6.99 watts.

Alternate Stepper Power Calculation Method #2

Further investigation into the impact of power supply voltage level (24 VDC versus 12 VDC) on stepper motor power requirements identified another method of stepper power estimation taking into account the power supply voltage level. The formula that takes power supply voltage into account is as follows:

Isc = (Vmot / Vps)*C* Iph*M

NEMA 17 Motor

Isc = Stepper Power Supply Load Current

Vmot = Stepper Phase Voltage : 2.8 VDC

Vps = Power Supply Voltage : 24 VDC

C = Number of Coils (Usually 2) : 2

Iph = Stepper Phase Current : 1.68 Amps

M = Margin of Safety : 1.5

Isc = (2.8/24)*2*1.68*1.5 = 0.588 amps (Drawn from 24 VDC PS)

This current would require 14.11 Watts at 24 VDC to be drawn from the 24 VDC power supply.

Comparing the two methods of stepper motor power consumption, it appears that major difference is that Method #2 includes a multiplier for the number of coils, in this case 2. Thus, if the coil multiplier was used in Method #1, the predicted power would be 13.97 watts, close to the 14.11 watts predicted by Method #2.Based upon this it is proposed that Method #2 be utilized to predict DC stepper motor current loads for power supply selection. In addition, I would propose a 75% Margin of Safety instead of the 50%.

Based upon the proposed Method #2 stepper power estimation formula, the following are estimates for our selected steppers:

X & Y Steppers (NEMA 23) P/N 23HM22-28045

Isc = (Vmot / Vps)*C* Iph*M

= (2.5/24)*2*2.8*1.75 = 1.02 amps from 24 VDC power supply (24.5 watts)

Z Steppers (NEMA 17) P/N 17HM19-16845

Isc = (Vmot / Vps)*C* Iph*M

= (2.77/24)*2*1.68*1.75 = 0.68 amps from 24 VDC power supply (16.29 watts)

Extruder Stepper (NEMA 17) P/N 17H54023

Isc = (Vmot / Vps)*C* Iph*M

= (4.1/24)*2*1*1.75 = 0.60 amps from 24 VDC power supply (14.35 watts)

Tool Stepper (NEMA 11) Not ID’d

Isc = (Vmot / Vps)*C* Iph*M

= (2.66/24)*2*0.95*1.75 = 0.37 amps from 24 VDC PS (8.84 watts)

STEPPER POWER REQUIRED

3 Z Steppers: 3*16.29 = 48.87 Watts

X and Y Steppers: 2*24.5 = 49 watts

Extruder Stepper: 14.35 watts

Tool Stepper: 8.84 watts

TOTAL 121.06 watts

EXTRUDER STEPPER (17HS4023)

Usongshine NEMA 17 Stepper Motor Bipolar Step Motor for Titan Extruder 3D Printer 4.1V 1A 13Ncm (18.4oz.in) 4 Lead 1.8 Deg with 1m Cable (17HS4023)

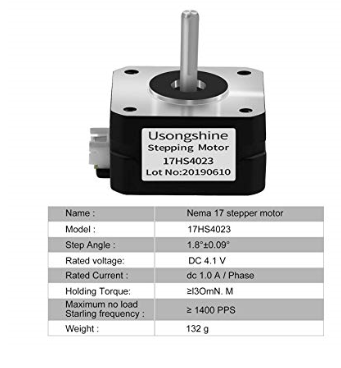
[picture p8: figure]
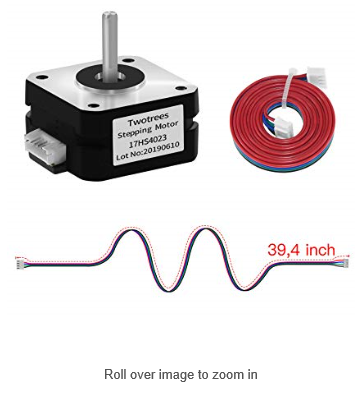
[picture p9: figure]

X, Y STEPPERS (23HM22-2804S)

STEPPERONLINE 0.9 deg NEMA 23 Step Motor Bipolar 1.26Nm (178.4oz.in) 2.8A 4-lead

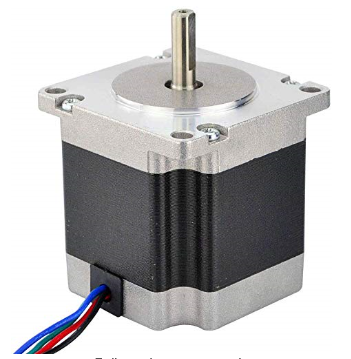
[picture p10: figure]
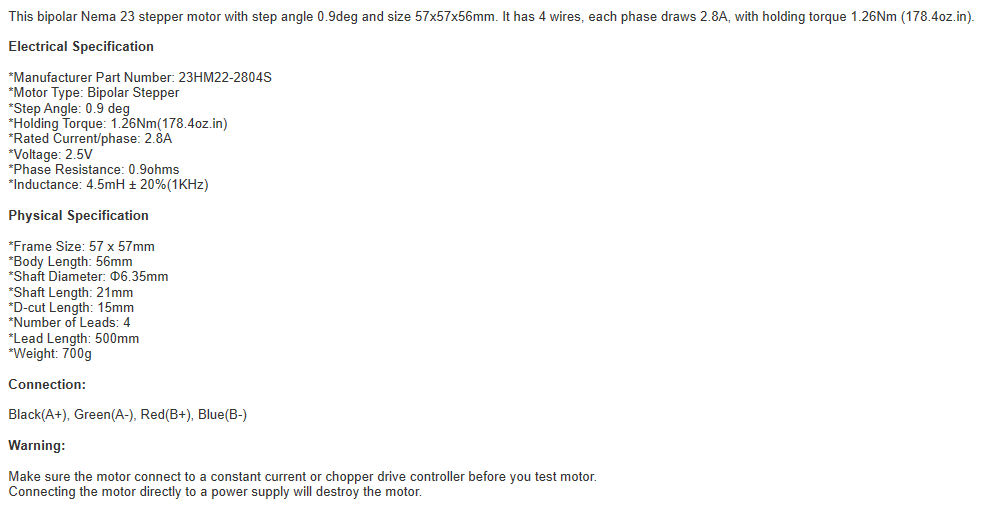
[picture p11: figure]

Z STEPPERS (17HM19-1684S)

# STEPPERONLINE NEMA 17 Bipolar Stepper 0.9deg (400 steps/rev) 1.68A 44Ncm (62.3oz.in) Motor

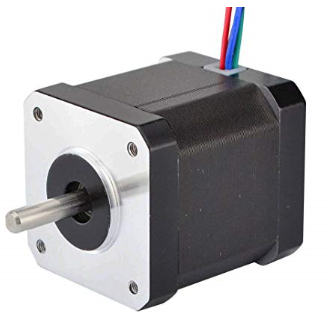
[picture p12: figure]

# OSM Technology Co., Ltd

. (https://www.amazon.com/s?search-alias=aps&field-keywords=OSM+Technology+Co.%2CLtd.)

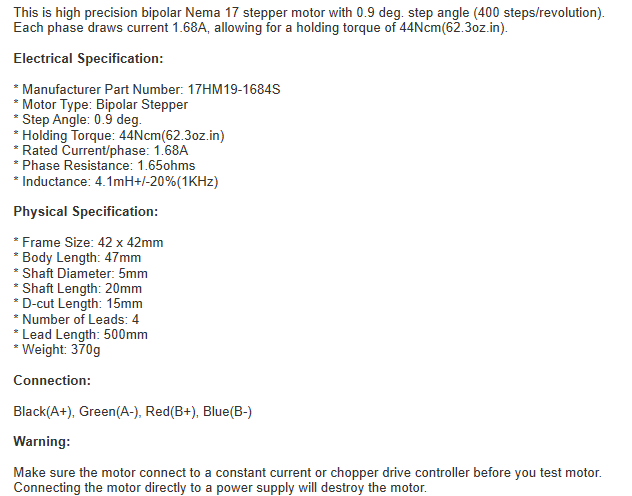
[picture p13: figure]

TOOL STEPPER

TBD

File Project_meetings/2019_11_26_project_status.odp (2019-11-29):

## ETA-DIY-BIG printer project

Meeting notes from 2019-11-26 meeting

## Summary

Agenda

1. Build "big decision flow chart" for the project.
2. Talk about a project name (I hate this part - someone please just pick a cool name)
3. Take a first crack a writing down the project goals and objectives.

Meeting Attendees:

Mike, Doug, Mark (came in late and reviewed our porposed decisions)

Meeting Notes

- We reviewed the “big decision” flow charts, discussed several of the decisions we need to make and have proposals for them. Each proposed decision is documented on it's own page and will be open for public review, discussion, ridicule, etc via Slack until the next meeting (12/3, 9am). Those pages follow directly. In addition, on the decision flow chart pages, these proposed decisions are highlighted in Orange.
- Project Name - One decision proposal we have is to highly leverage Mark McComsey's printer design (his 3rd printer design). Since this will be a derivative of that, we decided to call the project the “Mark4” in his honor.
- Project goals and objectives: We did a brief review, but there is probably more to be done here.
- Short term goal: We have a short term goal (next 1-2 weeks) to identify ~$1200 of materials we can buy that will have a low risk of not being eventually used. We need this “low risk” bit because the design is not finalized and will not be before the budgeted money will expire. Things go on the shopping list as decisions get made.

## Proposed Decisions

This section of the noted holds decisions we propose to lock in next week, including rationale. If you think we are heading in a wrong direction, please say something, including which other direction you think we should be heading.

## Location of printer?

Proposed decision:
Printer will be located where exhaust fumes can be taken outside the building – proposed site is on the table under the exhaust hood. Depth of this bench is 700mm.

Proposal date: 2019-11-26

Proposed ratification date: 2019-12-03

Rationale

- Many materials we would like to print off-gas unpleasant fumes and need to be ducted .

Concerns

- Space under the hood needs to be shared with the kiln and planned ceramic printer.
- When placed on the existing bench, the print area for lox Z-axis values ( first layers and short parts) may be too high for easy observation. We may need to have a lower platform for the printer and duct exhaust to the fume hood.

What material items does this decision allow us to purchase?

Next steps

- Collect feedback, ratify decision

## What printer style?

Proposed decision:
Build a Core XY style printer. Lots of leverage from an existing design.

Proposal date: 2019-11-26

Proposed ratification date: 2019-12-03

Rationale

- No movement of the part being built means less moving mass. Lower torques that would tend to trip the part off the build plate and/or oppose the motion intended by the motors.
- Why not Hbot? CoreXY designs are more stable than Hbot. Online reference (http://www.doublejumpelectric.com/projects/core_xy/2014-07-15-core_xy/)
- Why not cartesian? A cartesian has 2 moving rails (one on X and one on Y). This means more moving mass, and the challenges associated with mass.
- Lots of leverage of an existing design means less risk of costly changes being required to meet part quality objectives.

Concerns

What material items does this decision allow us to purchase?

Next steps

- Collect feedback, ratify decision

## Design leverage from where?

Proposed decision:
Make our design a close derivative of the printer Mark McComsey showed us on 11/24.

Proposal date: 2019-11-26

Proposed ratification date: 2019-12-03

Rationale

- Mark's design seems structurally very stable and robust.
- The Belt layout does not contain fundamental design errors of belts not parallel to rails.
- Mark has a design in Fusion 360 we can use.
- Mark has demonstrated the easy manufacturability of his component parts.

Concerns

- Mark is just getting started with his first prints now. What if changes are needed? We believe changes can be made without significant risk to materials we purchase.

What material items does this decision allow us to purchase?

- Aluminum plates for top and bottom (need to pick plate size)
- 4080 Aluminum extrusions for corner columns (need to pick a length)
- Garolite sheet 24" x 24" x 1/4" sheet for electronics mount

Next steps

- Collect feedback, ratify decision

## Project Name?

Proposed decision:
Name this printer “The Mark4”.

Proposal date: 2019-11-26

Proposed ratification date: 2019-12-03

Rationale

- Name is in honor of the high leverage from Mark McComsey's third printer design.

Concerns

What material items does this decision allow us to purchase?

Next steps

- Collect feedback, ratify decision

## Build Plate Size?

Proposed decision:
Printable area of 350mm (X) and 350mm (Y)

Proposal date: 2019-11-26

Proposed ratification date: 2019-12-03

Rationale

- This build plate size should enable printing of “helmet” sized objects

Concerns

- Mark's printable Y dimension is only 290mm. After discussing with Mark, he feels it will be easy to extend the Y by starting with a larger aluminum plate (24” x 24”)

What material items does this decision allow us to purchase?

- Aluminum plates for top and bottom (need to pick plate size)
- Aluminum plate for X-Bridge
- 4080 Aluminum extrusions for corner columns (need to pick a length)
- Garolite sheet 24" x 24" x 1/4" sheet for electronics mount
- X-Rails (400mm, track can be cut to shorter length if needed)
- Y-Rails (500mm – track can be cut to shorter length if needed)

Next steps

- Collect feedback, ratify decision

## Part Max Z-Height?

Proposed decision:
Max part size we can build inside Mark's frame design.

Proposal date: 2019-11-26

Proposed ratification date: 2019-12-03

Rationale

- Mark reports his printer is designed to build parts up to 400mm tall
- We have not locked in on a single-screw Z-axis support (vs 3 screw), but Mark's design supports a 500mm Z-screw, plus motor below it. We feel the frame materials that support this should allow us to build to the 400mm Mark achieved.

Concerns

What material items does this decision allow us to purchase?

- 4080 Aluminum extrusions for corner columns

Next steps

- Collect feedback, ratify decision

## Enclosed?

Proposed decision:
Printer will be enclosed, and thermally controlled. Follow Mark's direction, using polycarbonate “greenhouse” panels for sides, front, and top enclosure.

Proposal date: 2019-11-26

Proposed ratification date: 2019-12-03

Rationale

- An enclosed printer enables the area around the part to be maintained at a constant temperature, which should make more consistent parts.
- An enclosed printer enables management of fumes, allowing a wider range of materials to be printed.
- An enclosed printer reduces energy required to maintain the build plate temperature.

Concerns

- We will need a fan to mix cool air from outside the enclosure to maintain the internal temperature. Placement will be important to keep drafts from deforming a part while it is being printed.

What material items does this decision allow us to purchase?

- Polycarbonate sheet
- Exhaust fan

Next steps

- Collect feedback, ratify decision

## Document repository?

Proposed decision:
We will use the BARN github (https://github.com/BainbridgeArtisanResourceNetwork) as a repository for the documentation of the project, the design, and the operating manuals for the project.

Proposal date: 2019-11-26

Proposed ratification date: 2019-12-03

Rationale

- An enclosed printer enables the area around the part to be maintained at a constant temperature, which should make more consistent parts.
- An enclosed printer enables management of fumes, allowing a wider range of materials to be printed.
- An enclosed printer reduces energy required to maintain the build plate temperature.

Concerns

- We will need a fan to mix cool air from outside the enclosure to maintain the internal temperature. Placement will be important to keep drafts from deforming a part while it is being printed.

What material items does this decision allow us to purchase?

- Polycarbonate sheet
- Exhaust fan

Next steps

- Collect feedback, ratify decision

## Decision doc – Document repository

- 2019-11-26
  - Proposed decision: DIY a Core XY style printer
  - Rationale
  - Next steps
    - If not objections, will lock this at our next meeting.

## Topics for 12/3/2019

- This page starts a section of material to use in discussion of agenda topics for next week.
  - Which Extruder?
  - Include a Tool Changer?
  - Which electronics parts?

## Which Extruder/hotend?

Information:

Requirements

- Default extruder should be dual-material

Features we like:

- Dual gear drive
- Direct drive (vs bowden)

Recommendations:

- (From Mark) Bondtech BMG-X2 and Mosquito hot ends

## Include a tool-changer?

Information:

Requirements

- None

Features we like:

- A tool changer give flexibility for multiple materials
- Mark says his design can support the E3D tool changer (but he has not implemented it yet)

Recommendations:

- E3D style tool changer
- Jubilee “variant” of E3D tool changer

## Which Electronics?

Information:

Requirements

- Support all the motors, thermocouples, switches, PWM signals etc that we need.

Features we like:

- >8 bit

Recommendations:

- Duet2 + Paneldu touchscreen + (if needed) Duex 5 expander
- Duet3 + HDMI touchscreen

## Big decsion list – from proposal

- Design decisions
  - Build plate size
  - Max Z size
  - CoreXY belt layout (mostly pulley arrangement)
  - Idler pulley support (cantilever axles vs other, plate vs rails)
  - Motor mounting (direct vs coupler)
  - Motor selection (size)
  - Rail selection (linear vs something else) and placement.
  - Gantry design
  - Z-axis (single lead screw vs three)
  - Electronics (Duet 2 vs wait for Duet 3, UI)
  - Frame – anti-racking strength (hefty Al stock vs thinner stock with corner strengthening.
  - Manufactured mechanical pieces – 3D printed vs machined.
  - Power distribution and control.
  - Tool changer or permanent tool (and how many nozzles)
  - Extruder type (Bowden, direct drive)
  - Hot end selection
  - Enclosure design and thermal management.

## Project Goals

1. Create an ETA community project
2. Make an “industrial grade”, large capacity 3D printer for ETA studio users
- Big enough for helmets/masks
- High print quality and fast print speed
- Easy to use
- Easy to maintain
- Well documented

## Decision flow – Fundamentals

Printer Style == CoreXY

Documentation repository == github – Mike to GET A PROJECT CREATED.

Printable materials?

(Max bed temp)

(Max extruder temp)

Where does the printer

live in the studio?

Under fume hood.

min quality Print speed

PLA @ 100mm/sec

LEDs

Illumination?

Light show?

Design Leverage points

- Overall Layout == Mark McComsey's Design
- Tool changer (if used) == Jubilee (E3D variant)
- Belt Layout
- Other?

Video capture?

Telemetry?

## Analysis Core XY belt layout

- 2019-11-27 After the meeting
  - Good reference material
    - https://drmrehorst.blogspot.com/2018/08/corexy-mechanism-layout-and-belt.html
    - https://drmrehorst.blogspot.com/2017/07/ummd-corexy-mechanism.html
  - Rationale
  - Next steps
    - If not objections, will lock this at our next meeting.

## Decision flow – frame size

Yes

Build plate

Size?

Part

Max Z Height?

Z- Lift

One or three

motors

NEMA 17

or 23 motor(s)

Which face(es)?

Select

Lead-screw(s)

Buy

Lead-screw(s)

Volume?

Select

Shaft coupler(s)

Buy

Shaft coupler(s)

Buy Z Motors

material

Select

Z rails

Buy

Z rails

Build plate

Structure?

Z -Volume?

Required frame size

X =

Y =

Z =

Top plate size

Buy top plate

material

Buy bottom

plate

material

Buy Frame

material

Tool changer?

Select one

Which face?

Bottom

plate size

How many tools

Which tools?

Airflow plan

fan placement

Volume?

Select Frame

material

Enclosed?

Volume?

## Decision flow – Build plate

Build plate

Size?

Build plate

Style?

Bed heater

Style?

AC/DC?

Make/Buy?

Select

Build plate

Buy

build plate(s)

Select

Bed heater

Buy

Bed material

Buy

Bed heater

Select

Bed heater SSR

Buy

Bed heater SSR

Build plate

Structure?

Lift rough

design

Buy lift

material

## Decision flow – Build plate

Build plate

Size?

Build plate

Style?

Bed heater

Style?

AC/DC?

Make/Buy?

Select

Build plate

Buy

build plate(s)

Select

Bed heater

Buy

Bed material

Buy

Bed heater

Select

Bed heater SSR

Buy

Bed heater SSR

Build plate

Structure?

Lift rough

design

Buy lift

material

## Decision flow – XY mechanics

Rough Y-rail

location

Max

Y-rail length

Select Y-Rails

Buy Y-Rails

Belt layout?

Rough X-rail

location

Max

X-rail length

Select X-Rail

Buy X-Rail

Motor mount

rough design

Coupled/direct?

Idler pulley mount

rough design

Buy motor mount

material (couplers?)

Motor locations?

Idler pulley count

Toothed?

Smooth?

Buy idler pulley mount

material

Belt:

Width?

Material?

Belt motor

NEMA 17?

NEMA 23?

Steps?

Torque?

Buy idler pulleys

Buy belts

Buy X/Y motors

## Decision flow – Electronics

HW control board

8 vs 32 bit?

Select

controller board

Buy

controller board

Select

User Interface

Buy

User interface

Power budget

- Control board
- Bed heater
- XY motors
- Zmotor(s)
- Extruder(s)
- Hot end(s)
- LEDs
- (Enclosure cooling fan)
- PSU efficiency

Select

Power supply

Buy

Power supply

## Decision flow – X crossbar

Belt layout

Rough Gantry design

Buy

Materials for gantry

Buy

Materials for tool changer

If tool changing -

Tool holder selection

Extruder selection

Hot end selection

Buy

Extruder

Buy

Hot end

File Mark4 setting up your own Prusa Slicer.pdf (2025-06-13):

BARN TechLab | Adding the Mark4 to your Prusa Slicer Version 2.0 | Page 1/4

# Adding the Mark4 to your

# Prusa Slicer

### Overview

Setting up your own Prusa Slicer to support the Mark4 takes a few steps, but following those steps will get the printer, with it's preferred settings, print profiles, and filaments available to you. We'll improve this guide as we learn better ways to do it.

Step 1 – Download required files from the BARN github repository.
1 Click this like to open the github repository so | you can download the file: link to file Click the download icon to download the file. This file (slicer ini files.zip) is a compressed file containing the files you'll need.
2 Extract the file to the right location on your | computer. On windows machines, you can right-click on the slicer ini files.zip in your file Manager, and select Extract All… The location is: C:\users\<youruser>\AppData\Roaming\Prusa Slicer\vendor Where <youruser> is your user directory name.
3 | This will add two files and a directory to the vendor directory. The TechLab directory will contain three files | NEW NEW

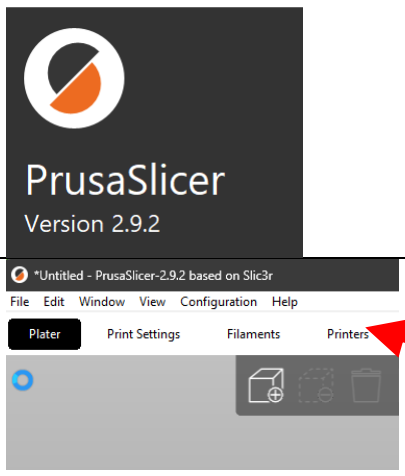
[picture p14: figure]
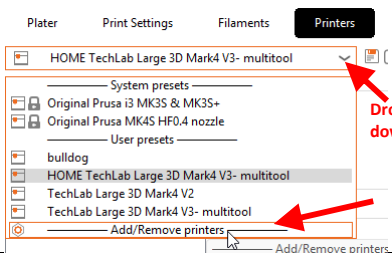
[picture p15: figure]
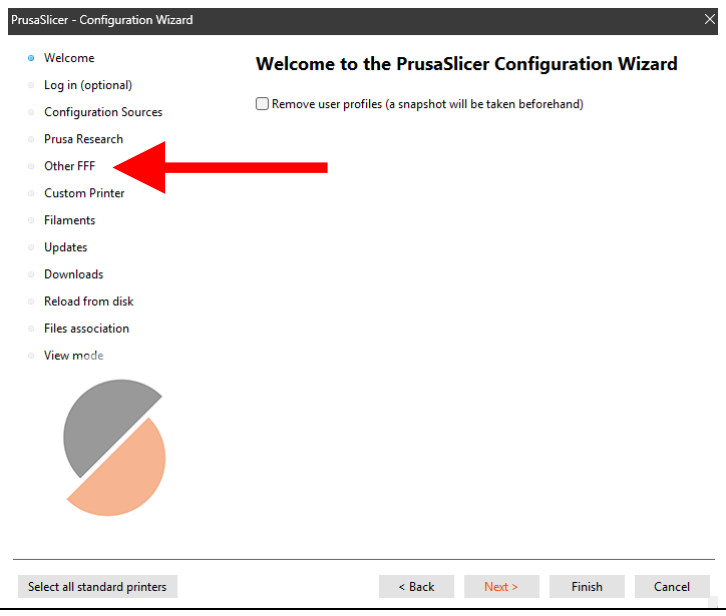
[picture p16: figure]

BARN TechLab | Adding the Mark4 to your Prusa Slicer Version 2.0 | Page 2/4

### Step 2 – Install the Mark4 Printer in Prusa Slicer

### 1 Start PrusaSlicer on your computer. If it is not

Version 2.9.0 or higher, please update it
before proceeding.

### 2 Go to the Printers Tab

Pull down the dropdown menu with the printers list and select "Add/Remove Printers" at the bottom. This will start the PrusaSlicer Configuration Wizard.

### Step 3 – Adding the Mark 4 in the Configuration Wizard

### 1 Once the Configuration Wizard starts (it'll take

a few seconds longer than you'd expect), Click
on "Other FFF"

Drop
down

Printers
Tab

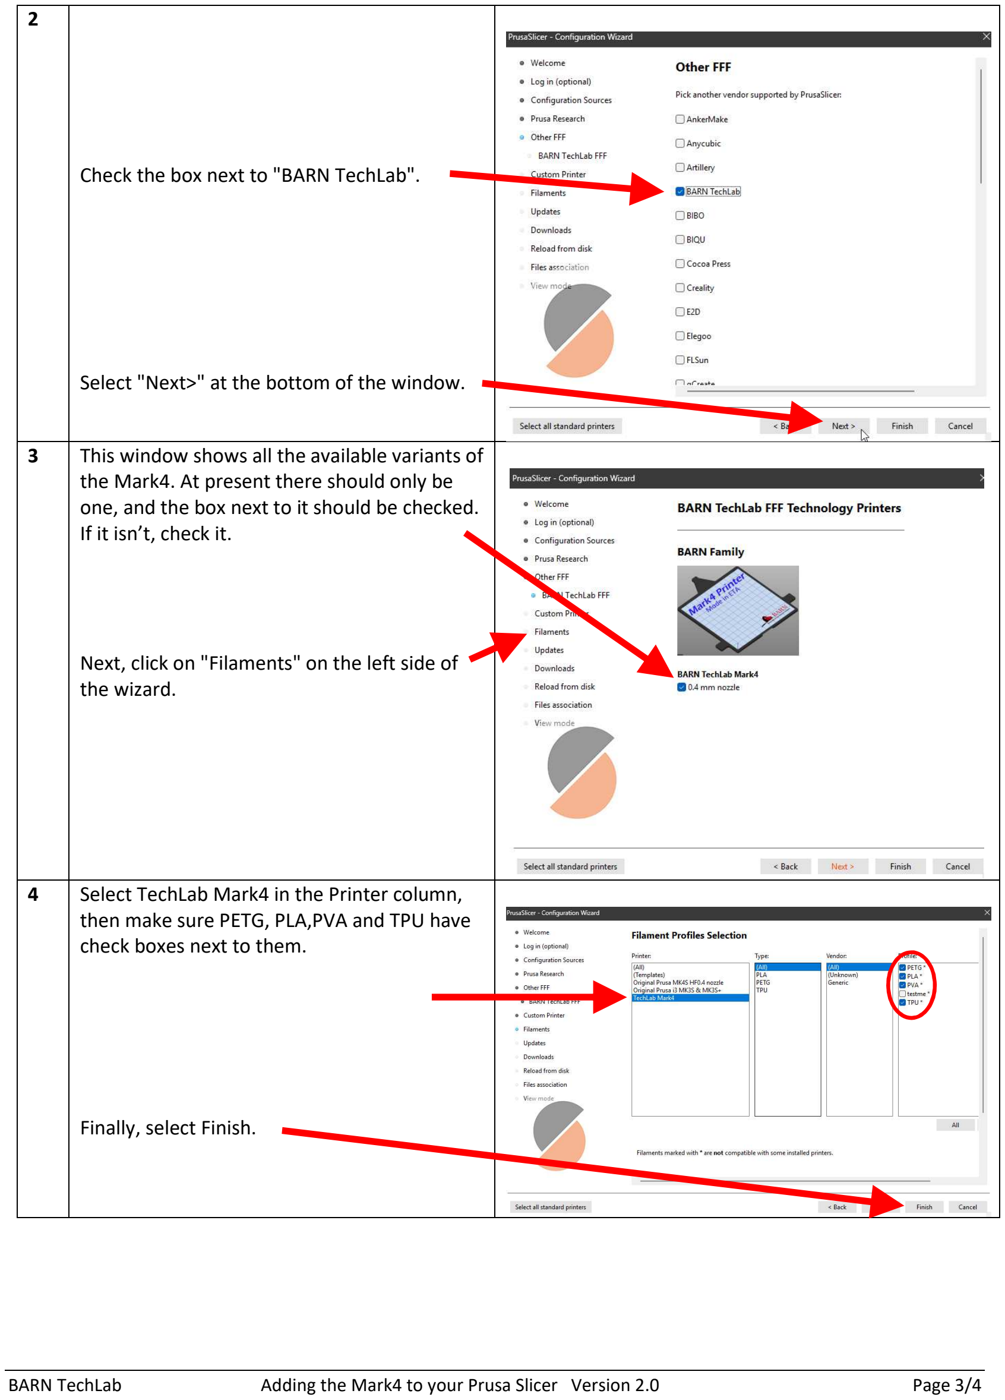
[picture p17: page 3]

BARN TechLab | Adding the Mark4 to your Prusa Slicer Version 2.0 | Page 3/4
2 | Check the box next to "BARN TechLab". Select "Next>" at the bottom of the window.
3 This window shows all the available variants of | the Mark4. At present there should only be one, and the box next to it should be checked. If it isn’t, check it. Next, click on "Filaments" on the left side of the wizard.
4 Select TechLab Mark4 in the Printer column, | then make sure PETG, PLA,PVA and TPU have check boxes next to them. Finally, select Finish.

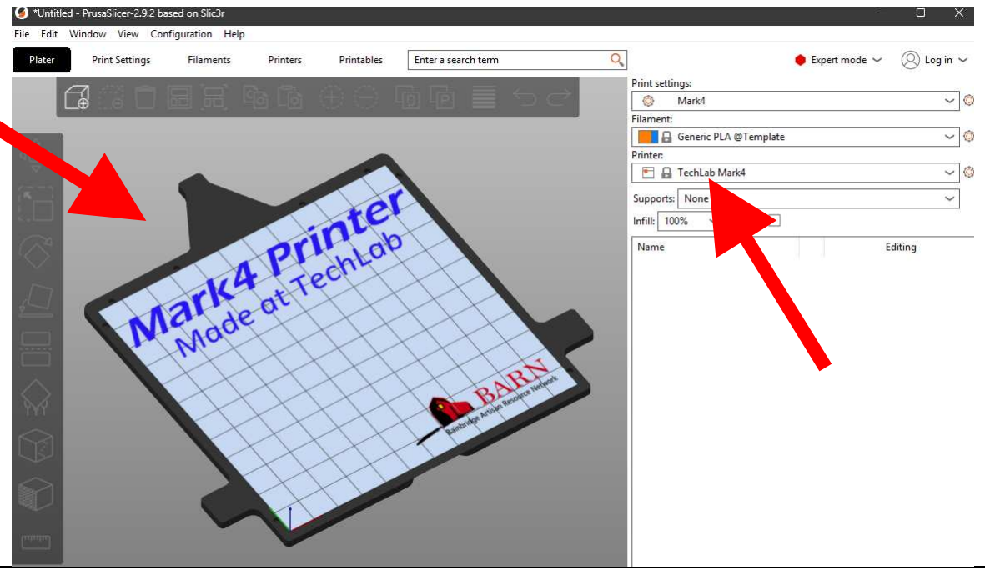
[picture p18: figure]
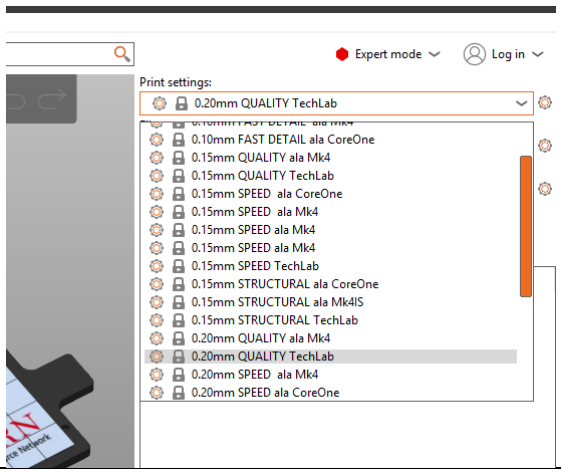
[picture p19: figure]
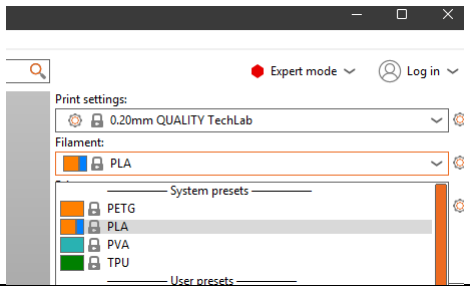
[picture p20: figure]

BARN TechLab | Adding the Mark4 to your Prusa Slicer Version 2.0 | Page 4/4

### Step 3 – verify it worked

1 Go to the Plater tab in Prusa Slicer. | You should see the Mark 4's build plate and artwork when TechLabMark4 is selected in the Printer options. You should also see TechLab Mark4 in the Printer options
2 | You should see a bunch of Print Setting Options in the dropdown on this window too. The choices that end in "TechLab" are optimized for the Mark4.
3 | You should also see the Mark 4 default filament options. in the Filament Dropdown.

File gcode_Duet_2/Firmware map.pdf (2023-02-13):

### Duet fw boots

- Attempt to connect to network
- If sys/runonce.g is present, run it, then delete it.
- If sys.daemon.g is present, run every 10 seconds in an
asynchronous thread.
- Wait for commands to execute.
- Run sys/config.g

### sys/config.g

Main file for configuring the FW to run our machine.

- Configures Duet board fw for our machine configuration.
- motor parameters
- limit switches
- network parameters
- BLTouch Z probe
- bed heater parameters
- Runs other macro files to configure each tool. At present, tool #0 is not yet in it's own file, but tool 1 is.
- There are some parameters that need to be set for all tools with a single command and they are in config.g.

Creates a global variable used by daemon.g for setting wifi.

Files required by Duet Files created by BARN

sys/tool_0_config.g

We made this macro because ther are a lot of commands to set up a tool and we wanted to reduce the clutter in config.g
- Configures duet board for tool0
- motor, extruder, heater parameters
- fans (part/extruder)
- Calls sys/tool0_Z_offset.g. to set the Z-offset for tool0.

sys/create_global variables.g Declares global variables we use elsewhere so we don't need to test for their existence before using them.

sys/runonce.g
Not used by us

sys/daemon.g
We have code that looks to see if wifi is connected, then stops it fron trying after a few attempts.

# Automatic at power-on

sys/tool_1_config.g

Same as tool_0_config.g, but for tool #1

sys/tool0_Z_offset.g
Contains only a G10 command to set the Z offset for this tool. It is a separate file to enable macros for easily adjusting the offset.
See macros/prepare.

sys/tool1_Z_offset.g
Same as tool0_Z_offset, but for tool #1

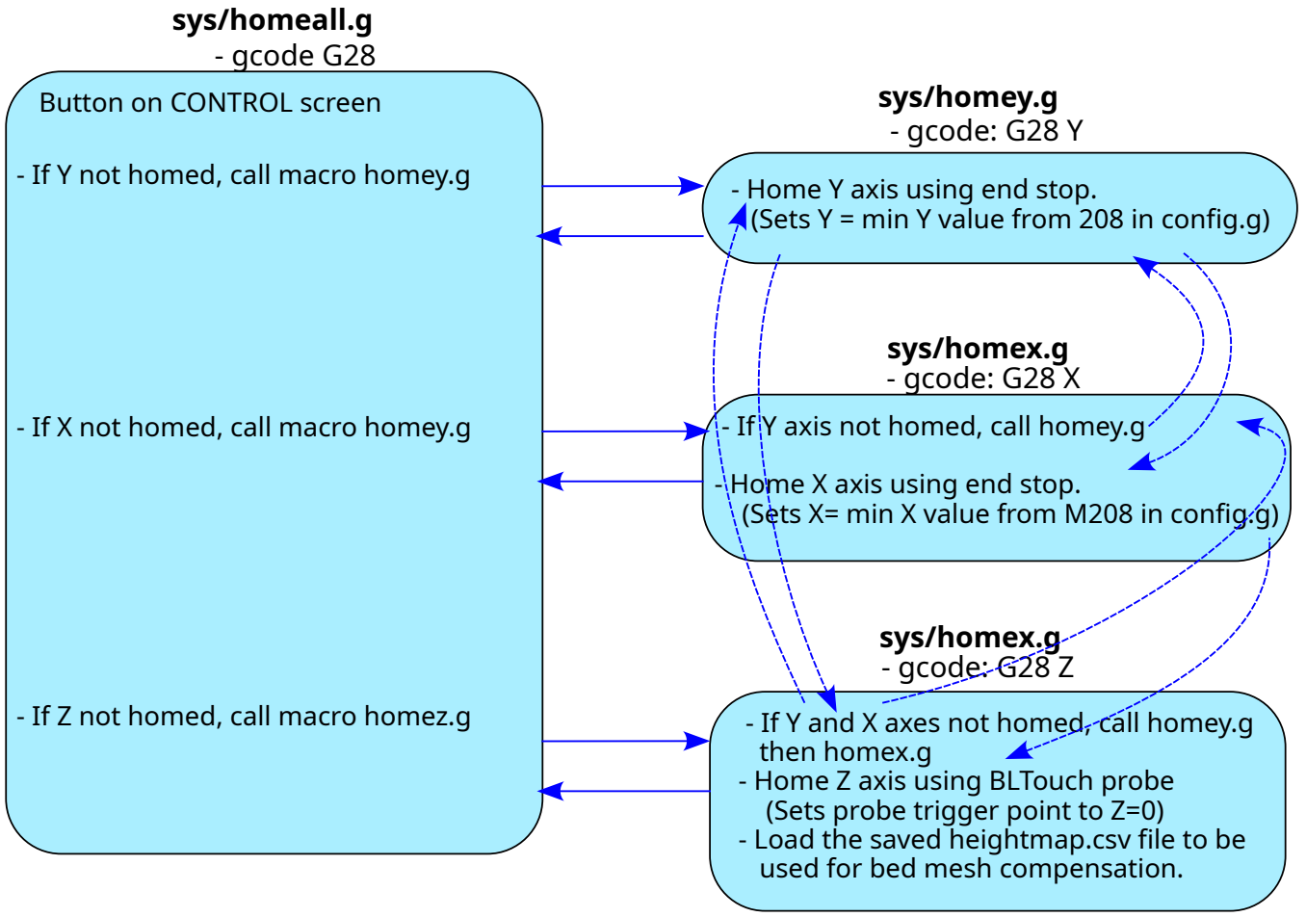
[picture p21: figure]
then homex.g - Home Z axis using BLTouch probe (Sets probe trigger point to Z=0); used for bed mesh compensation.; sys/homex.g - gcode: G28 Z; - Home Y axis using end stop.; sys/homey.g - gcode: G28 Y; sys/homeall.g - gcode G28 Button on CONTROL screen; - If Y not homed, call macro homey.g; - If X not homed, call macro homey.g; - If Z not homed, call macro homez.g; - If Y axis not homed, call homey.g; - Home X axis using end stop.; sys/homex.g - gcode: G28 X

- If Y and X axes not homed, call homey.g
- Load the saved heightmap.csv file to be

(Sets Y = min Y value from 208 in config.g)

Files required by Duet Files invented by BARN

# User initiated after power-on

(Sets X= min X value from M208 in config.g)

Adjust the Z axis lead screws to make the bed as level as possible.
- Disable bed compensation mesh
- After leveling, re-home Z axis

sys/bed.g
- gcode: G32

Runs G29 S0 to create and enable a new bed mesh.
We wrote this macro because there is not a button on the control panel for it.

macros/prepare/create mesh_G29_S0.g
- gcode: G29 S02

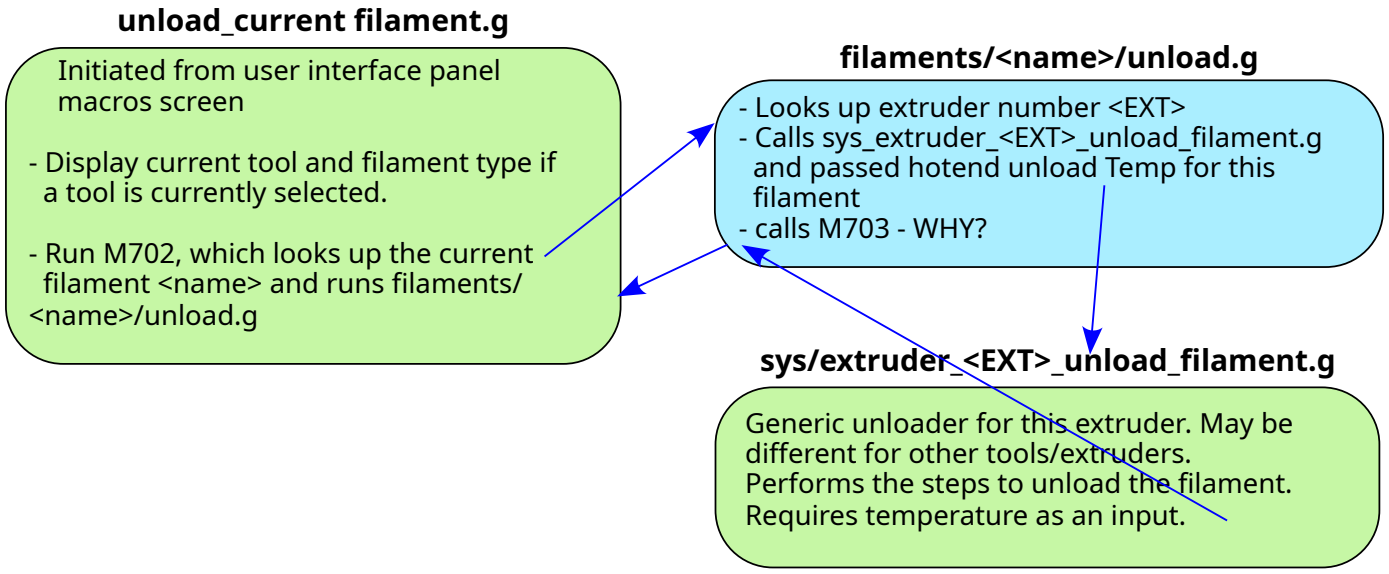
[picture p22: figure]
sys/extruder_<EXT>_unload_filament.g; different for other tools/extruders.; Requires temperature as an input.; filaments/<name>/unload.g - Looks up extruder number <EXT>; and passed hotend unload Temp for this filament - calls M703 - WHY?; unload_current filament.g Initiated from user interface panel macros screen; a tool is currently selected.; - Run M702, which looks up the current filament <name> and runs filaments/ <name>/unload.g

Generic unloader for this extruder. May be Performs the steps to unload the filament.

- Calls sys_extruder_<EXT>_unload_filament.g
- Display current tool and filament type if

# Filament Change Macros

### All are located in the Macros/load_unload_filaments directory

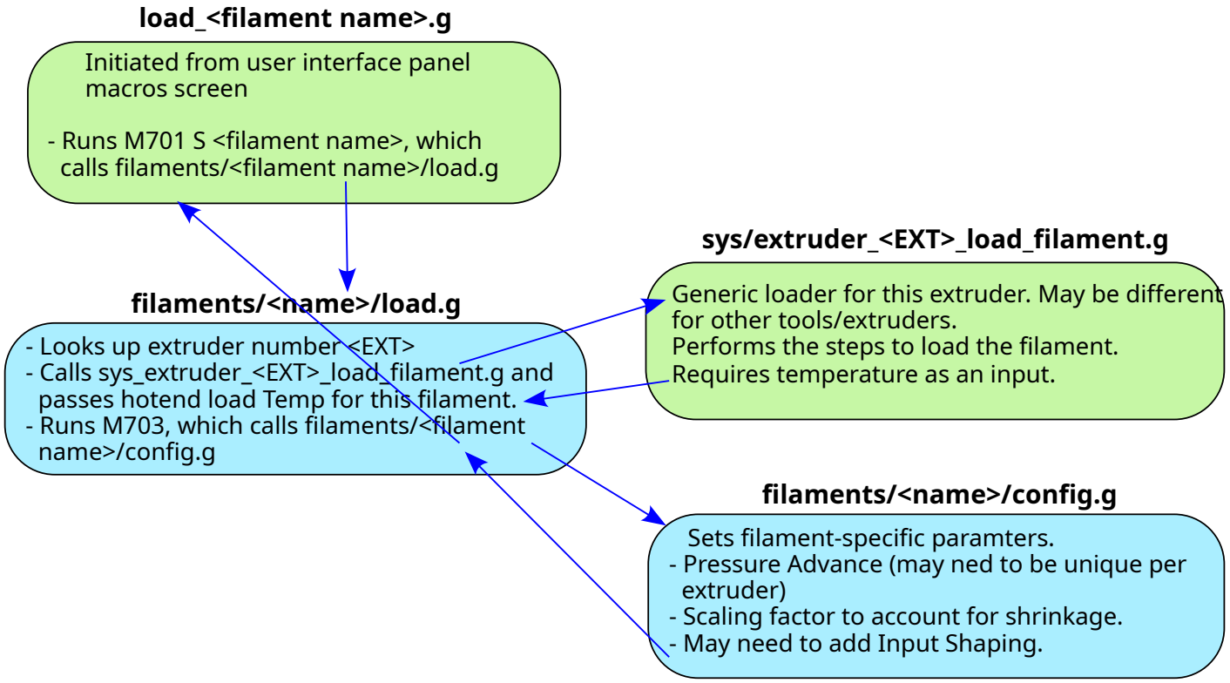
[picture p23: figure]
sys/extruder_<EXT>_load_filament.g; for other tools/extruders.; Requires temperature as an input.; filaments/<name>/load.g - Looks up extruder number <EXT>; name>/config.g; load_<filament name>.g Initiated from user interface panel macros screen; - Runs M701 S <filament name>, which calls filaments/<filament name>/load.g; filaments/<name>/config.g Sets filament-specific paramters.; extruder); - May need to add Input Shaping.

Generic loader for this extruder. May be different Performs the steps to load the filament.
- Calls sys_extruder_<EXT>_load_filament.g and passes hotend load Temp for this filament.
- Runs M703, which calls filaments/<filament
- Pressure Advance (may ned to be unique per
- Scaling factor to account for shrinkage.

sys/tfree0.g

Actions to do with tool 0 before it is released.
- Park the tool, set temperatures to standby, turn off fans?

# Tool Change Macros

sys/tpre0.g

Actions to do with a new tool before tool 0 is selected
- ??

sys/tpost0.g

Actions to take with a new tool after it is selected
- Grab tool with tool changer.
- Turn on heaters and fans
- Unretract filament and wipe?
- Return to starting location?

sys/start.g
If present, run before sunning print file gcode. We added:
- Collect time for start of print.
- Collect name of file to be printed

# Printing Macros

print file from slicer
Required:
- Sliced for Mark4 printer.
- Slicer must select a tool.
- M0 at end of job
Optional:
- Home all axes
- Create height map
- Pauses

Required
- M0 at end of job

sys/resume.g
If present, run when a print is resumed after a pause. The default has:
- Go back to the print location, return to the
previous print move, unretract the filament.

sys/cancel.g
If present, run when a print is cancelled. We do not have this file at present.

sys/pause.g
If present, run when file has a pause or the print is paused form the printer interface.
The default has:
- Drop the bed, retract a bit of filament, move
the print head to a known location

sys/stop.g
If present, run when file has M0 at end of job. We added:
- Capture print end time.
- Log start, end times and print name to file.
- Drop the bed, retract the filament, move print head out of the way, turn off heaters and fans.

allow cold extrude.g
Runs M302 P1 to allow the extruder motor to turn even if the hot end is not hot

# Debug Macros

### All are located in the Macros/debug directory

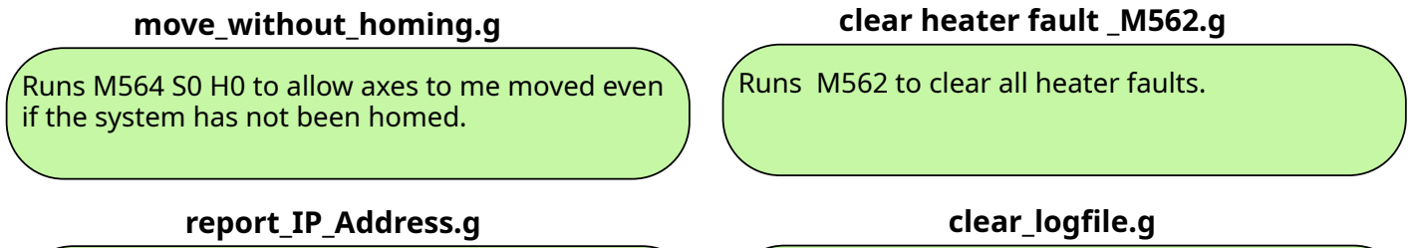
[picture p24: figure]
clear heater fault _M562.g; Runs M562 to clear all heater faults.; clear_logfile.g; move_without_homing.g; if the system has not been homed.; report_IP_Address.g

Pauses logging, deletes the file: m sys/eventlog.g

Runs M564 S0 H0 to allow axes to me moved even

Print a messagfe showing the IP Address of the

# Print Prep Macros

### All are located in the Macros/prepare directory

create mesh.g
Runs M29 S0 which is the bed mesh creation and loading command.

fold baby steps into tool offset.g Used to adjust the Z-offset for the current tool, based on the current baby steps setting.
- Looks up the current tool tool, it's Z offset and current baby steps setting.
- Calculates a new z-offset requiring no baby steps.
- Creates a new sys/tool<N>_Z_offset.g file
- changes the z offset amd zeros out the babysteps.

adj tool z_offset.g
Used to set the Z-offset for the current tool.
- User makes Z moves until the nozzle measures 0.2mm above the build plate (using feeler gauges)
- Calculates the Z-offset requiring to make this location 0.2mm after the offset is applied.
- Creates a new sys/tool<N>_Z_offset.g file

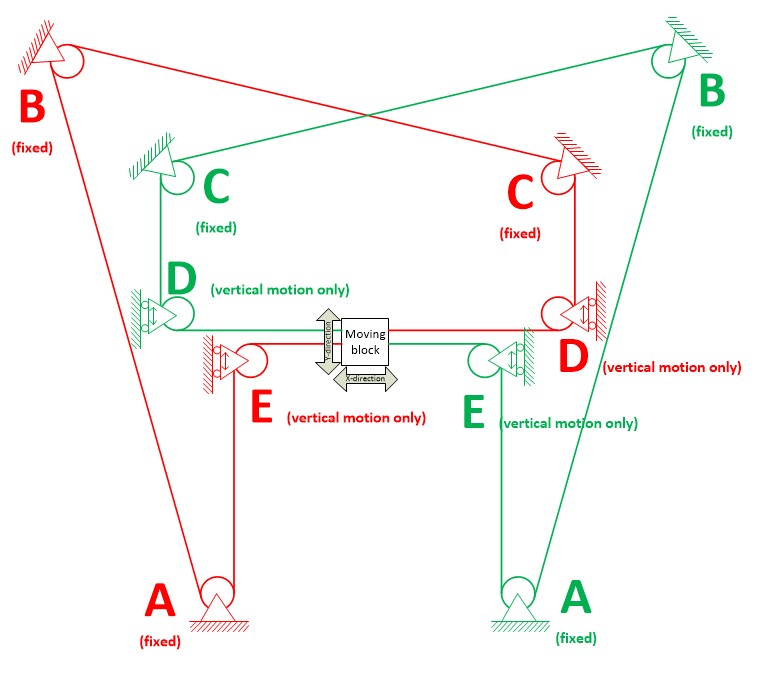
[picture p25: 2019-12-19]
Fusion360_model/images/wiki_generic_belt_design.jpg

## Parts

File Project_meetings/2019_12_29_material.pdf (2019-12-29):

12/29 design review meeting

Belt layout

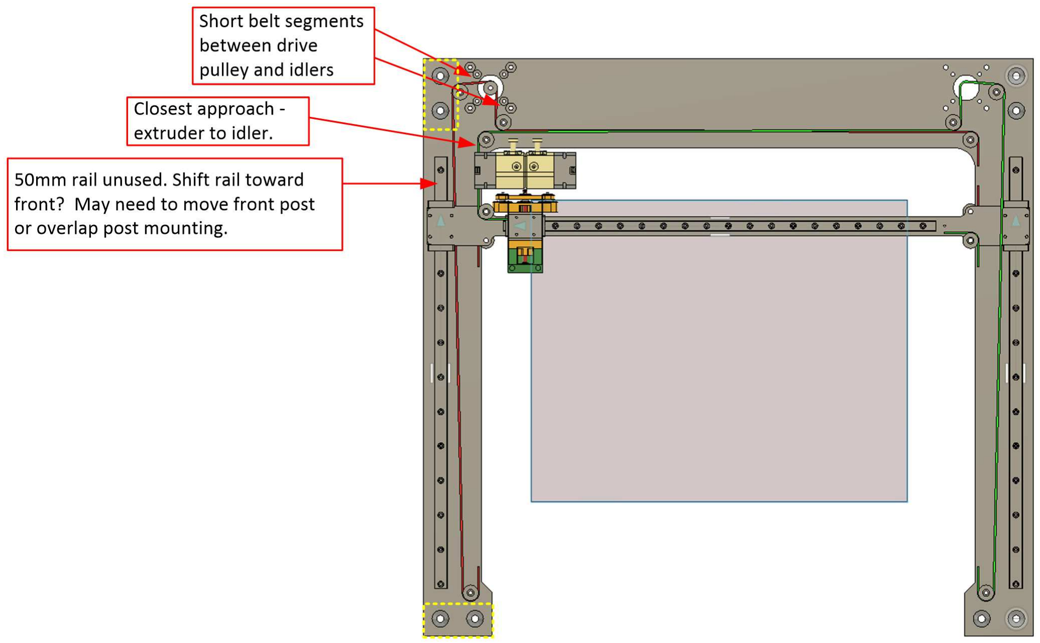
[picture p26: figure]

Alternate Belt Layout #1

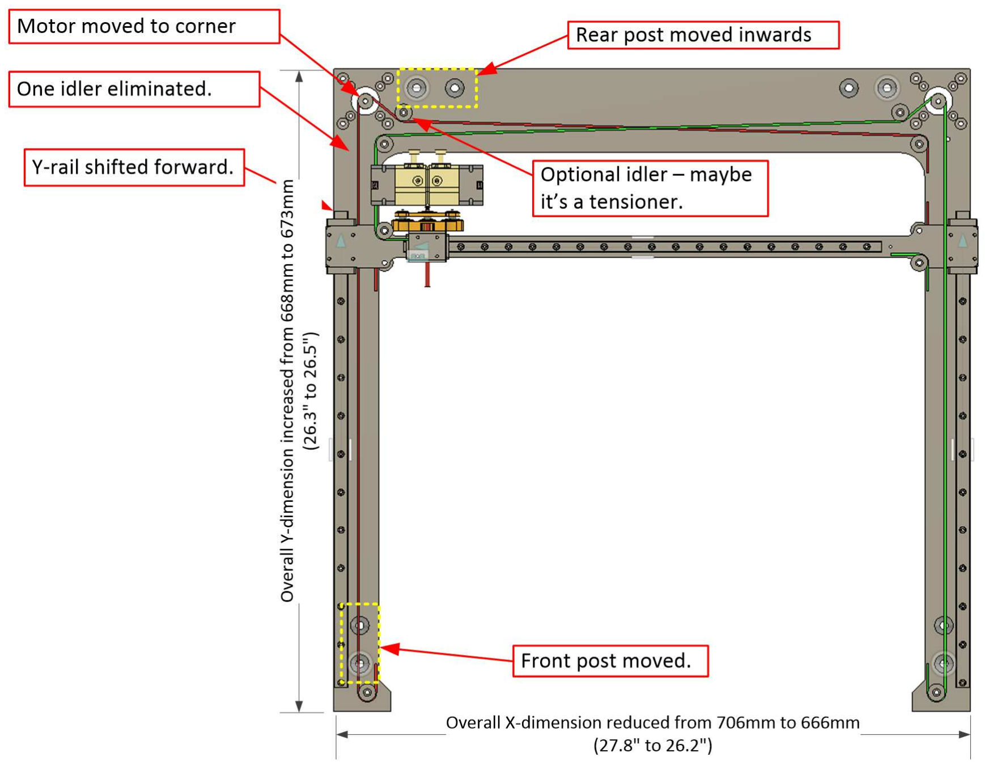
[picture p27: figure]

Belt Layout comparison

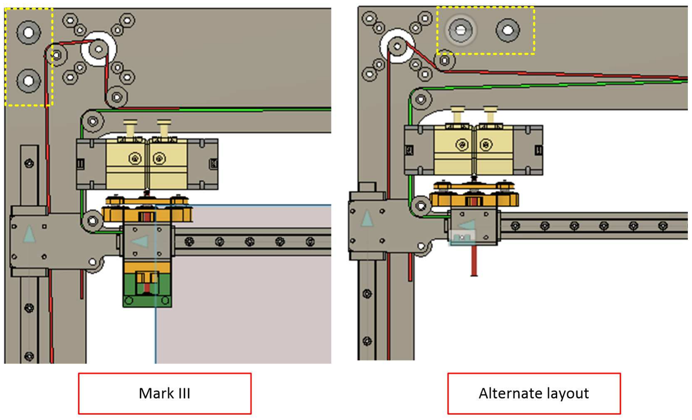
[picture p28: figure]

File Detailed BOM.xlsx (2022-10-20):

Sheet: Propose to buy now
PARTS PROPOSED FOR PURCHASE NOW
propose to buy now | x
Supplier | Part Number | Description | quantity on-hand | extended quantity | Quantity to purchase | Cost each | shipping | Tax | Web-link | Sum of Buy-now costs | Sum of Cost of excess material
Amazon.com | A-0050 | Printer 3D Parts, FYSETC 12" x 12" x 0.3" 3D Printer Heated Bed Insulation Lightweight Foam Foil Self-Adhesive Insulation Mat | 0 | 1 | 1 | 10.99 | 0 | $0.99 | https://www.amazon.com/FYSETC-Insulation-Lightweight-Self-Adhesive-Ultimaker/dp/B07DWPYQDS | $0.00 | $0.00
 | A-0058 | Inkbird Solid State Relay 40DA DC SSR Black Heat Sink for PID Thermostat Temperature Controller | 0 | 1 | 1 | 13.99 | 0 | $1.26 | https://www.amazon.com/dp/B01MCWO35P | $0.00 | $0.00
(blank) | A-0081 | Hotend thermistor | 0 | 1 | 1 | (blank) | 0 | $0.00 | (blank) | $0.00 | $0.00
Grand Total |  |  |  |  |  |  |  |  |  | $0.00 | $0.00

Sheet: Not yet ordered
PARTS NOT YET ORDERED
Supplier | Description | Part Number | extended quantity | quantity on-hand | Quantity on order | Quantity to purchase | Sum of Remaining ideal cost | Sum of Cost of excess material
aliexpress | Cloned 7i PanelDue Touch Screen Controller For BLV MGN Cube | A-0073 | 1 | 0 | 0 | 1 | $63.64 | $0.00
Amazon.com | 1/2 inch PET Expandable Braided Sleeving – Black 25 ft | A-0097 | 1 | 0 | 0 | 1 | $7.55 | $0.00
 | 1/4 inch PET Expandable Braided Sleeving – Black 25 ft | A-0096 | 1 | 0 | 0 | 1 | $7.42 | $0.00
 | 4" zip ties | A-0094 | 1 | 0 | 0 | 200 | $0.03 | $6.50
 | Bearing, Flange F606ZZ, 6mm x 17mm x 6mm | A-0003 | 28 | 20 | 0 | 10 | $11.76 | $2.94
 | Cooling Fan for 3D Printer, 4020 DC 40×40×20mm Turbo Fan | A-0080 | 1 | 0 | 0 | 2 | $5.12 | $5.12
 | FYSETC 3D Printer Ender 3 Parts 4010 DC 24V Cooling Fan | A-0079 | 1 | 0 | 0 | 2 | $5.99 | $5.99
 | Inkbird Solid State Relay 40DA DC SSR Black Heat Sink for PID Thermostat Temperature Controller | A-0058 | 1 | 0 | 0 | 1 | $15.25 | $0.00
 | Printer 3D Parts, FYSETC 12" x 12" x 0.3" 3D Printer Heated Bed Insulation Lightweight Foam Foil Self-Adhesive Insulation Mat | A-0050 | 1 | 0 | 0 | 1 | $11.98 | $0.00
 | RGB Wire Line Cord 22AWG 4pin 22 Gauge - 20M | A-0098 | 1 | 0 | 0 | 1 | $9.48 | $0.00
 | Tie Mount 0.75 Inch 20mm Black Samll Squares Adhesive Mounting | A-0095 | 1 | 0 | 0 | 100 | $0.10 | $9.70
digikey | Heated Bed 10K Lug Ring Thermistor (PN NTC/BC2891-ND) | A-0074 | 1 | 0 | 0 | 1 | $3.28 | $0.00
 | Mechanical limit switch ( SS0750300F070P1A ) | A-0077 | 1 | 0 | 0 | 1 | $1.20 | $0.00
 | SSR Protective cover | A-0075 | 1 | 0 | 0 | 1 | $5.56 | $0.00
ebay | 1/2" x 1/8" Disc - SmCo - Samarium Cobalt Rare Earth Magnet, Grade N30 | A-0070 | 36 | 0 | 0 | 40 | $48.49 | $5.39
midwest steel supply | 1/4" cast aluminum plate 3" x 22" | A-0017 | 1 | 0 | 0 | 1 | $0.00 | $0.00
reprapworld.com | GT2x9 mm Kevlar-reinforced timing belt | A-0038 | 5 | 0 | 0 | 5 | $36.29 | $0.00
(blank) | E3D High Precision Ceramic Heater Cartridge 24V 30W | A-0078 | 1 | 0 | 0 | 1 | $19.60 | $0.00
 | Hotend thermistor | A-0081 | 1 | 0 | 0 | 1 | $0.00 | $0.00
 | NEMA 11 Stepper with gearing | A-0076 | 1 | 0 | 0 | 1 | $0.00 | $0.00
 | Z-height sensor | A-0082 | 1 | 0 | 0 | 1 | $0.00 | $0.00
Grand Total |  |  |  |  |  |  | $252.75 | $35.63

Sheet: Parts on-order
PARTS ON ORDER (but not yet received)
Supplier | Description | Part Number | Quantity on order | quantity on-hand | Order date | Due date | Sum of Ideal cost of parts on order | Sum of Cost of excess material
Grand Total

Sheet: Parts on-hand
PARTS ON HAND
 |  |  |  |  |  |  |  | 158.0916807
Supplier | Part Number | Description | quantity on-hand | Quantity donated | Sum of Ideal cost of parts on hand | Sum of Cost of excess material | Sum of Actual cost | Vale of donated items
aliexpress | A-0051 | 350 x 350mm Flex Spring Steel Sheet Pre-Applied PEI | 1 | (blank) | $47.27 | $0.00 | $47.27 | 0
 | A-0054 | Mellow All Metal NF-Crazy Hotend V6 Copper Nozzle For Ender 3 CR10 Prusa I3 MK3S Alfawise Titan/Bmg Extruder 3D Printer Part | 1 | (blank) | $67.98 | $0.00 | $67.98 | 0
 | A-0055 | Cloned Duet 2 Wifi V1.04 DuetWifi Advanced 32 Bit Electronics | 1 | 1 | $88.96 | $0.00 | $0.00 | 88.96
 | A-0056 | Cloned Duex5 Expansion Board Controller With TMC2660 Stepper Motor Driver Fit Thermocouple PT100 VS Duet 2 Wifi 3D Printer Parts | 1 | (blank) | $78.48 | $0.00 | $78.48 | 0
Amazon.com | A-0003 | Bearing, Flange F606ZZ, 6mm x 17mm x 6mm | 20 | 20 | $29.41 | $2.94 | $0.00 | 29.4082
 | A-0004 | uxcell 6063 Aluminum Round Tube 300mm Length 12.7mm OD 6mm Inner Dia Seamless Aluminum Straight Tubing 2 Pcs | 314 | (blank) | $5.81 | $5.30 | $0.00 | 0
 | A-0005 | K & S PRECISION METALS 251 .010x4x10 BRS SHT Metal | 15 | 15 | $3.59 | $0.24 | $0.00 | 3.588825
 | A-0007 | Washer, M6, 304 stainless, OD 12mm, .9mm thick | 36 | 36 | $1.59 | $0.00 | $0.00 | 1.587258
 | A-0008 | 0.9 deg Nema 23 Step Motor Bipolar 1.26Nm(178.4oz.in) 2.8A 4-lead, 6.35 shaft dia | 2 | (blank) | $76.69 | $0.00 | $76.69 | 0
 | A-0009 | uxcell 6063 Aluminum Round Tube 300mm Length 12mm OD 5mm Inner Dia Seamless Aluminum Straight Tubing | 353 | 600 | $12.94 | $9.06 | $0.00 | 12.94109767
 | A-0013 | BALITENSEN 4 pcs 2GT 20 teeth Timing Pulley bore 6.35 for GT2 belt width 10mm for CNC 3D printer(GT2 20teeth) | 2 | (blank) | $6.27 | $6.27 | $12.54 | 0
 | A-0018 | M3 Thread T-Nut for 40 Series European Aluminium Profile Hammer Head | 39 | (blank) | $9.63 | $2.72 | $12.35 | 0
 | A-0019 | 0.9deg Nema 17 Stepper Motor Bipolar 2A 46Ncm/65oz.in 42x42x48mm 4-Wires DIY CNC | 3 | (blank) | $70.30 | $0.00 | $45.70 | 0
 | A-0027 | Sliding T Slot Nuts 4040 Series M5 26 Pack T Nuts Carbon Steel | 9 | (blank) | $3.05 | $5.77 | $8.82 | 0
 | A-0049 | 350 X 350mm(Approx. 14" x 14"), 110V 800W, with 3M PSA & NTC 100K thermistor, KEENOVO Silicone Heater Mat/Pad, Huge Large 3D Printer HeatBed Build Plate Heater | 1 | (blank) | $76.29 | $0.00 | $76.29 | 0
 | A-0052 | Redrex Dual Drive BMG Bowden Extruder High Performance Upgrading Parts (no motor) | 1 | (blank) | $26.15 | $0.00 | $26.15 | 0
 | A-0053 | Usongshine Nema 17 Stepper Motor Bipolar Step Motor for Titan Extruder 3D Printer 4.1V 1A 13Ncm | 1 | (blank) | $10.88 | $0.00 | $10.88 | 0
 | A-0057 | EAGWELL 24v 15a DC Universal Regulated Switching Power Supply 360w | 1 | (blank) | $31.26 | $0.00 | $31.26 | 0
 | A-0083 | AC 115/250VAC 10A Noise Suppressing Power Entry Module | 1 | (blank) | $16.34 | $0.00 | $16.34 | 0
 | A-0084 | AC Power cord | 1 | (blank) | $6.70 | $0.00 | $6.70 | 0
 | A-0086 | microswitch (bridge) | 4 | (blank) | $6.90 | $3.45 | $10.35 | 0
 | A-0089 | White Stranded #16 Insulated Wire (120VAC & 24 VDC Distribution)(25 Feet) | 1 | (blank) | $7.51 | $0.00 | $7.51 | 0
 | A-0090 | Black Stranded #16 Insulated Wire (120VAC Distribution)(25 Feet) | 1 | (blank) | $7.51 | $0.00 | $7.51 | 0
 | A-0091 | Green Stranded #16 Insulated Wire (120VAC Distribution)(25 Feet) | 1 | (blank) | $7.51 | $0.00 | $7.51 | 0
 | A-0092 | Red Insulated Stranded #16 Wire (24 VDC Distribution)(25 Feet) | 1 | (blank) | $7.51 | $0.00 | $7.51 | 0
banggood | A-0011 | Machifit 500mm Length MGN15 Linear Rail Guide with MGN15H Linear Rail Block | 5 | (blank) | $150.00 | $0.00 | $67.62 | 0
 | A-0016 | 400mm MGN12 Linear Rail Guide with MGN12H Carriage Block | 1 | (blank) | $19.98 | $0.00 | $19.98 | 0
 | A-0021 | Machifit MGN12C Linear Rail Block for MGN12 Linear Rail Guide | 1 | (blank) | $8.99 | $0.00 | $8.99 | 0
bolt depot | A-0006 | M6-1.0 x 60mmbutton head Screw | 4 | (blank) | $2.81 | $0.00 | $2.81 | 0
 | A-0010 | M5 x 65mm 12.9 Alloy Steel Hex Socket Head Cap Screws Bolt Black | 4 | (blank) | $1.93 | $0.00 | $1.93 | 0
 | A-0012 | M3-0.5x30mm Socket Head Cap Bolts Screws, 304 Stainless Steel 18-8, Allen Socket Drive, Fully Machine Thread, Bright Finish | 65 | (blank) | $8.18 | $4.41 | $12.59 | 0
 | A-0015 | M8 x 1.25 socket cap screw, 30mm long | 12 | (blank) | $3.96 | $0.00 | $3.96 | 0
 | A-0022 | M6 x 1.0mm Nylon Inserted Hex Lock Nuts 304 Stainless Steel | 22 | (blank) | $1.50 | $5.31 | $6.81 | 0
 | A-0026 | M5-0.8 x 16mm Button Head Socket Cap Screws | 8 | (blank) | $1.32 | $0.00 | $1.32 | 0
 | A-0029 | M6 x 65mm Button Head Cap Screws Metric, Grade 12.9 Alloy Steel Black Oxide | 4 | (blank) | $2.04 | $0.00 | $2.04 | 0
 | A-0030 | M5-0.8 X 75MM Socket Head Cap Screws, Black Oxide Coated Steel | 4 | (blank) | $2.42 | $0.00 | $2.42 | 0
 | A-0031 | M6 Flat/Countersunk Head Socket Screws (M6 x 22mm) | 2 | (blank) | $0.50 | $0.00 | $0.50 | 0
 | A-0032 | M6-1.0 x 35mm Flat Head Socket Screws | 2 | (blank) | $0.55 | $0.00 | $0.55 | 0
 | A-0033 | M3-0.5x20mm Socket Head Cap Bolts Screws, 304 Stainless Steel 18-8, Allen Socket Drive, Fully Machine Thread, Bright Finish | 20 | (blank) | $1.61 | $6.45 | $8.06 | 0
 | A-0034 | M3 x 0.5mm 304 Stainless Steel Self-Lock Nylon Inserted Hex Lock Nuts, | 46 | (blank) | $2.02 | $2.37 | $4.39 | 0
 | A-0035 | M3x6mmx0.5mm Stainless Steel Flat Washer | 46 | (blank) | $0.70 | $0.82 | $1.51 | 0
 | A-0040 | M4 x 0.7mm 304 Stainless Steel Nylon Lock Nuts | 6 | (blank) | $0.30 | $4.66 | $4.95 | 0
 | A-0041 | M4x12mmx1 mm Stainless Steel Round Flat Washer | 30 | (blank) | $0.52 | $1.20 | $1.72 | 0
 | A-0061 | M4 x 10mm Alloy Steel Hex Bolt Socket Head Cap Screws | 12 | (blank) | $1.65 | $0.00 | $1.65 | 0
 | A-0062 | M5x10mmx1mm Stainless Steel Metric Round Flat Washer | 9 | (blank) | $0.22 | $2.22 | $2.44 | 0
 | A-0063 | M6 x 25mm button head screw | 8 | (blank) | $1.76 | $0.00 | $1.76 | 0
 | A-0071 | M8 flat washers, Stainless steel 18-8 | 12 | (blank) | $1.32 | $0.00 | $1.32 | 0
digikey | A-0072 | SSR Thermal Pad | 1 | (blank) | $1.45 | -$1.45 | $0.00 | 0
 | A-0085 | Dual Row 4 Position Covered Screw Terminal Strip 600V 25A | 1 | (blank) | $4.63 | $0.00 | $4.63 | 0
 | A-0087 | Quick Disconnect Terminal, 0.25in x 0.032in, 14-16 AWG (Power Entry Module) | 10 | (blank) | $5.17 | $0.00 | $5.17 | 0
 | A-0088 | Ring Terminal Crimp Connector (24 VDC Terminals) | 10 | (blank) | $3.19 | $0.00 | $3.19 | 0
jjwinco.com | A-0036 | DIN 319 Ball Knob, .63" diameter, M4 threaded hole | 3 | 3 | $21.61 | $0.00 | $0.00 | 21.6063
mcmaster-carr | A-0093 | White Stranded #26 Insulated Wire (Thermistor, Limit Switches)(100 Feet) | 1 | (blank) | $17.97 | $0.00 | $17.97 | 0
midwest steel supply | A-0001 | 3/8" thick Cast aluminum plate, 28" x 24" | 1 | (blank) | $121.61 | $0.00 | $121.11 | 0
 | A-0002 | 3/8" thick T6061 Aluminum plate, 28" x 24" | 1 | (blank) | $121.61 | $0.00 | $121.11 | 0
misumi | A-0014 | 40x80 Aluminum Extrusion - 8 Series, Base 40, 625mm long, both ends tapped, with helicoil inserts | 3 | (blank) | $132.61 | $0.00 | $132.61 | 0
online metals | A-0023 | T6061 Al Angle extrusion 2.5" x 2.5" x .25 thick, 3" long | 3 | 3 | $14.31 | $4.77 | $0.00
 | A-0024 | Aluminum angle 2" x 2" x .25" thick, 12" long | 1 | (blank) | $0.93 | $0.00 | $0.00
 | A-0025 | T 6061 Al Angle extrusion 2" x 2" x .125" 6" aluminum (for side ball mount) | 2 | (blank) | $9.51 | $0.00 | $9.51
 | A-0045 | Aluminum angle 2.5" x 2.5" x .25" x 100mm | 3 | 3 | $16.35 | $0.00 | $0.00
 | A-0064 | Aluminum bar .75 square, 12" long | 12 | 12 | $4.72 | $1.57 | $0.00
zyltech | A-0020 | 8mm T8x2 Lead Screw Trapezoidal ACME w/ Small Delrin Anti-Backlash Nut kit | 3 | (blank) | $65.51 | $0.00 | $65.51
 | A-0060 | Flexible Couplings 5mm to 8mm NEMA 17 Shaft Coupler | 3 | (blank) | $15.27 | $0.00 | $15.27
Grand Total |  |  |  |  | $1477.25 | $68.06 | $1213.24

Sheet: Parts
 |  |  |  |  |  |  |  |  |  | Ideal total cost |  |  |  |  |  |  |  |  |  |  | Remainnig SPEND cost
 |  |  |  |  |  |  |  |  |  | $1804.27 |  |  |  |  | $1477.25 |  | $0.00 |  |  | $334.53 | $401.80 | $240.40 |  |  |  |  | Comments | $0.00
Part Number | Description | Supplier | Cost | shipping | Tax | Web-link | Minimum order quantity | Comments | extended quantity | Ideal cost | propose to buy now | Quantity purchased | Quantity donated | quantity on-hand | Ideal cost of parts on hand | Quantity on order | Ideal cost of parts on order | Quantity to purchase | leftover material | Remaining ideal cost | Remaining Extended cost | Cost of excess material | Actual cost | Order date | Due date | received date | comments2 | Buy-now costs
A-0001 | 3/8" thick Cast aluminum plate, 28" x 24" | midwest steel supply | $100.60 | $21.02 | $0.00 | https://www.midweststeelsupply.com/store/castaluminumplateatp5 | 1 | $102.54 for 23 x 28 (minimum needed) | 1 | 121.61 |  | 1.00 |  | 1 | $121.61 | 0 | $0.00 | 0 | 0 | $0.00 | $0.00 | $0.00 | $121.11 | 2020-03-09 | 2020-03-20 | 2020-03-20 |  | $0.00
A-0002 | 3/8" thick T6061 Aluminum plate, 28" x 24" | midwest steel supply | $100.60 | $21.02 | $0.00 | https://www.midweststeelsupply.com/store/castaluminumplateatp5 | 1 |  | 1 | 121.61 |  | 1.00 |  | 1 | $121.61 | 0 | $0.00 | 0 | 0 | $0.00 | $0.00 | $0.00 | $121.11 | 2020-03-09 | 2020-03-20 | 2020-03-20 |  | $0.00
A-0003 | Bearing, Flange F606ZZ, 6mm x 17mm x 6mm | Amazon.com | $1.35 | $0.00 | $0.12 | https://www.amazon.com/gp/product/B07P3HNCCK | 10 | Purchase in packs of 10 | 28 | 41.17 |  | 0.00 | 20.00 | 20 | $29.41 | 0 | $0.00 | 10 | 2 | $11.76 | $14.70 | $2.94 |  |  |  |  | Mike donation - 20 pcs | $0.00
A-0004 | uxcell 6063 Aluminum Round Tube 300mm Length 12.7mm OD 6mm Inner Dia Seamless Aluminum Straight Tubing 2 Pcs | Amazon.com | $0.02 | $0.00 | $0.0015285 | https://www.amazon.com/uxcell-Aluminum-12-13mm-Seamless-Straight/dp/B07YCHFN8F | 300 | Price per mm | 313.8 | 5.81 |  | 600.00 |  | 314 | $5.81 | 0 | $0.00 | 0 | 286.2 | $0.00 | $0.00 | $5.30 | $0.00 |  |  |  | Mike donation | $0.00
A-0005 | K & S PRECISION METALS 251 .010x4x10 BRS SHT Metal | Amazon.com | $0.22 | $0.00 | $0.02 | https://www.amazon.com/PRECISION-METALS-251-010x4x10-Metal/dp/B004QB5Y3C | 40 | price per sq in | 14 | 3.35 |  | 0.00 | 15.00 | 15 | $3.59 | 0 | $0.00 | 0 | 1 | $0.00 | $0.00 | $0.24 | $0.00 |  |  |  | Mike donation | $0.00
A-0006 | M6-1.0 x 60mmbutton head Screw | bolt depot | $0.51 | $0.13 | $0.06 | https://www.boltdepot.com/Product-Details.aspx?product=6653 | 1 |  | 4 | 2.81 |  | 4.00 |  | 4 | $2.81 |  | $0.00 | 0 | 0 | $0.00 | $0.00 | $0.00 | $2.81 | 2020-02-14 | 2020-02-24 | 2020-02-24 | on order 2/14 | $0.00
A-0007 | Washer, M6, 304 stainless, OD 12mm, .9mm thick | Amazon.com | $0.04 | $0.00 | $0.0036405 | https://www.amazon.com/gp/product/B018TG8B8E | 200 |  | 36 | 1.59 |  | 0.00 | 36.00 | 36 | $1.59 | 0 | $0.00 | 0 | 0 | $0.00 | $0.00 | $0.00 | $0.00 |  |  |  | mike donation | $0.00
A-0008 | 0.9 deg Nema 23 Step Motor Bipolar 1.26Nm(178.4oz.in) 2.8A 4-lead, 6.35 shaft dia | Amazon.com | $35.18 | $0.00 | $3.17 | https://www.amazon.com/STEPPERONLINE-Bipolar-1-26Nm-178-4oz-4-lead/dp/B07DV91Z2M | 1 |  | 2 | 76.69 |  | 2.00 |  | 2 | $76.69 | 0 | $0.00 | 0 | 0 | $0.00 | $0.00 | $0.00 | $76.69 | 2020-02-21 | 3/13 - 4/1 | 2020-02-28 |  | $0.00
A-0009 | uxcell 6063 Aluminum Round Tube 300mm Length 12mm OD 5mm Inner Dia Seamless Aluminum Straight Tubing | Amazon.com | $0.03 | $0.00 | $0.003027 | https://www.amazon.com/uxcell-Aluminum-12-13mm-Seamless-Straight/dp/B07YCGPLHV | 300 | Price per mm | 353 | 12.94 |  | 0.00 | 600.00 | 353 | $12.94 | 0 | $0.00 | 0 | 247 | $0.00 | $0.00 | $9.06 | $0.00 |  |  |  | Mike donation | $0.00
A-0010 | M5 x 65mm 12.9 Alloy Steel Hex Socket Head Cap Screws Bolt Black | bolt depot | $0.35 | $0.09 | $0.04 | https://www.boltdepot.com/Product-Details.aspx?product=6532 | 1 |  | 4 | 1.93 |  | 4.00 |  | 4 | $1.93 |  | $0.00 | 0 | 0 | $0.00 | $0.00 | $0.00 | $1.93 | 2020-02-14 | 2020-02-24 | 2020-02-24 | on order 2/14 | $0.00
A-0011 | Machifit 500mm Length MGN15 Linear Rail Guide with MGN15H Linear Rail Block | banggood | $26.94 | $0.00 | $3.06 | https://www.banggood.com/Machifit-500mm-Length-MGN15-Linear-Rail-Guide-with-MGN15H-Linear-Rail-Block-CNC-Tool-p-1239196.html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 | 1 | Free shipping | 5 | 150.00 |  | 5.00 |  | 5 | $150.00 | 0 | $0.00 | 0 | 0 | $0.00 | $0.00 | $0.00 | $67.62 | 2020-02-29 |  | 2020-03-18 | Qty 3 Purchased 12/19 | $0.00
A-0012 | M3-0.5x30mm Socket Head Cap Bolts Screws, 304 Stainless Steel 18-8, Allen Socket Drive, Fully Machine Thread, Bright Finish | bolt depot | $0.09 | $0.02 | $0.01 | https://www.boltdepot.com/Product-Details.aspx?product=13641 | 100 |  | 65 | 8.18 |  | 100.00 |  | 65 | $8.18 |  | $0.00 | 0 | 35 | $0.00 | $0.00 | $4.41 | $12.59 | 2020-02-14 | 2020-02-24 | 2020-02-24 | on order 2/14 | $0.00
A-0013 | BALITENSEN 4 pcs 2GT 20 teeth Timing Pulley bore 6.35 for GT2 belt width 10mm for CNC 3D printer(GT2 20teeth) | Amazon.com | $2.88 | $0.00 | $0.26 | https://www.amazon.com/BALITENSEN-Timing-Pulley-printer-20teeth/dp/B079BNZDRZ | 4 |  | 2 | 6.27 |  | 4.00 |  | 2 | $6.27 | 0 | $0.00 | 0 | 2 | $0.00 | $0.00 | $6.27 | $12.54 | 2020-02-15 |  |  | ordered 2/15 | $0.00
A-0014 | 40x80 Aluminum Extrusion - 8 Series, Base 40, 625mm long, both ends tapped, with helicoil inserts | misumi | $38.68 | $5.52 | $0.00 | https://us.misumi-ec.com/vona2/detail/110302690310/?Tab=wysiwyg_area_0 | 1 |  | 3 | 132.61 |  | 3.00 |  | 3 | $132.61 | 0 | $0.00 | 0 | 0 | $0.00 | $0.00 | $0.00 | $132.61 | 2020-02-16 | 2020-02-28 | 2020-02-28 | on order 2/16 | $0.00
A-0015 | M8 x 1.25 socket cap screw, 30mm long | bolt depot | $0.24 | $0.06 | $0.03 | https://www.boltdepot.com/Product-Details.aspx?product=6563 | 1 | Shipping estimated $5 total | 12 | 3.96 |  | 12.00 |  | 12 | $3.96 |  | $0.00 | 0 | 0 | $0.00 | $0.00 | $0.00 | $3.96 | 2020-02-14 | 2020-02-24 | 2020-02-24 | on order 2/14 | $0.00
A-0016 | 400mm MGN12 Linear Rail Guide with MGN12H Carriage Block | banggood | $16.99 | $2.99 | $0.00 | https://www.banggood.com/Machifit-MGN12-100-1000mm-Linear-Rail-Guide-with-MGN12H-Linear-Sliding-Guide-Block-CNC-Parts-p-1156260.html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 | 1 | ordered 2/13 | 1 | 19.98 |  | 1.00 |  | 1 | $19.98 | 0 | $0.00 | 0 | 0 | $0.00 | $0.00 | $0.00 | $19.98 | 2020-02-14 |  | 2020-02-20 | ordered 2/14, received 2/20 | $0.00
A-0017 | 1/4" cast aluminum plate 3" x 22" | midwest steel supply | $0.00 | $0.00 | $0.00 | https://www.midweststeelsupply.com/store/castaluminumplateatp5 | 1 | Get out of center offcut of part A-0001 | 1 | 0.00 |  |  |  | 0 | $0.00 | 0 | $0.00 | 1 | 0 | $0.00 | $0.00 | $0.00 |  |  |  |  |  | $0.00
A-0018 | M3 Thread T-Nut for 40 Series European Aluminium Profile Hammer Head | amazon.com | $0.23 | $0.00 | $0.02 | https://www.amazon.com/gp/product/B07CN161T5 | 50 | Shipping estimated | 39 | 9.63 |  | 50.00 |  | 39 | $9.63 | 0 | $0.00 | 0 | 11 | $0.00 | $0.00 | $2.72 | $12.35 | 2020-02-21 | 2020-03-23 |  |  | $0.00
A-0019 | 0.9deg Nema 17 Stepper Motor Bipolar 2A 46Ncm/65oz.in 42x42x48mm 4-Wires DIY CNC | Amazon.com | $21.50 | $0.00 | $1.93 | https://www.amazon.com/gp/product/B00W9A2L3S | 1 |  | 3 | 70.30 |  | 3.00 |  | 3 | $70.30 | 0 | $0.00 | 0 | 0 | $0.00 | $0.00 | $0.00 | $45.70 |  |  |  | Purchased 12/19. ordered 1 more 2/15 | $0.00
A-0020 | 8mm T8x2 Lead Screw Trapezoidal ACME w/ Small Delrin Anti-Backlash Nut kit | zyltech | $16.95 | $3.36 | $1.53 | http://www.zyltech.com/8mm-t8x2-lead-screw-trapezoidal-acme-w-small-delrin-anti-backlash-nut-kit-custom-length-up-to-1000mm/ | 1 |  | 3 | 65.51 |  | 3.00 |  | 3 | $65.51 | 0 | $0.00 | 0 | 0 | $0.00 | $0.00 | $0.00 | $65.51 |  |  |  | ordered 2/13, received 2/20 | $0.00
A-0021 | Machifit MGN12C Linear Rail Block for MGN12 Linear Rail Guide | banggood | $8.99 | $0.00 | $0.00 | https://www.banggood.com/Machifit-MGN12C-Linear-Rail-Block-for-MGN12-Linear-Rail-Guide-CNC-Tool-p-1240120.html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 | 1 | Shipping estimated | 1 | 8.99 |  | 1.00 |  | 1 | $8.99 | 0 | $0.00 | 0 | 0 | $0.00 | $0.00 | $0.00 | $8.99 | 2020-02-13 | 2020-03-15 | 2020-03-20 | on order 2/13, shipped 2/19 | $0.00
A-0022 | M6 x 1.0mm Nylon Inserted Hex Lock Nuts 304 Stainless Steel | bolt depot | $0.05 | $0.01 | $0.01 | https://www.boltdepot.com/Product-Details.aspx?product=4795 | 100 | 5.9mm tall | 22 | 1.50 |  | 100.00 |  | 22 | $1.50 |  | $0.00 | 0 | 78 | $0.00 | $0.00 | $5.31 | $6.81 | 2020-02-14 | 2020-02-24 | 2020-02-24 | on order 2/14 | $0.00
A-0023 | T6061 Al Angle extrusion 2.5" x 2.5" x .25 thick, 3" long | online metals | $3.69 | $0.75 | $0.33 |  | 4 | For z-axis motor mounts, shipping estimated | 2 | 9.54 |  | 0.00 | 3.00 | 3 | $14.31 | 0 | $0.00 | 0 | 1 | $0.00 | $0.00 | $4.77 | $0.00 |  |  |  | mike donation | $0.00
A-0024 | Aluminum angle 2" x 2" x .25" thick, 12" long | online metals | $0.63 | $0.25 | $0.06 |  | 12 | Shipping estimated | 0 | 0.00 |  |  |  | 1 | $0.93 | 0 | $0.00 | 0 | 0 | $0.00 | $0.00 | $0.00 |  |  |  |  |  | $0.00
A-0025 | T 6061 Al Angle extrusion 2" x 2" x .125" 6" aluminum (for side ball mount) | online metals | $2.29 | $2.07 | $0.39 | https://www.onlinemetals.com/en/buy/angle?q=%3Aname-asc%3AAlloy%3A6061&checkbox=on&sort=name-asc# | 2 | For left and right kinematic ball holders on z-axis | 2 | 9.51 |  | 2.00 |  | 2 | $9.51 | 0 | $0.00 | 0 | 0 | $0.00 | $0.00 | $0.00 | $9.51 |  |  |  | on order 2/16 | $0.00
A-0026 | M5-0.8 x 16mm Button Head Socket Cap Screws | bolt depot | $0.12 | $0.03 | $0.01 | https://www.boltdepot.com/Product-Details.aspx?product=13345 | 1 |  | 8 | 1.32 |  | 8.00 |  | 8 | $1.32 |  | $0.00 | 0 | 0 | $0.00 | $0.00 | $0.00 | $1.32 | 2020-02-14 | 2020-02-24 | 2020-02-24 | on order 2/14 | $0.00
A-0027 | Sliding T Slot Nuts 4040 Series M5 26 Pack T Nuts Carbon Steel | Amazon.com | $0.31 | $0.00 | $0.03 | https://www.amazon.com/dp/B082F7B1QH | 26 |  | 9 | 3.05 |  | 26.00 |  | 9 | $3.05 | 0 | $0.00 | 0 | 17 | $0.00 | $0.00 | $5.77 | $8.82 | 2020-02-15 |  | 2020-02-18 | ordered 2/15 | $0.00
A-0028 | M4-0.70 x 14mm Button Head Socket Cap Bolts Screws, 18-8 Stainless Steel, Allen Hex Drive | Amazon.com | $0.09 | $0.00 | $0.01 | https://www.amazon.com/M4-0-70-Button-Stainless-Fullerkreg-Plastic/dp/B07H14FRRB | 100 |  | 0 | 0.00 |  |  |  | 0 | $0.00 | 0 | $0.00 | 0 | 0 | $0.00 | $0.00 | $0.00 |  |  |  |  |  | $0.00
A-0029 | M6 x 65mm Button Head Cap Screws Metric, Grade 12.9 Alloy Steel Black Oxide | bolt depot | $0.37 | $0.10 | $0.04 | https://www.boltdepot.com/Product-Details.aspx?product=18967 | 1 |  | 4 | 2.04 |  | 4.00 |  | 4 | $2.04 |  | $0.00 | 0 | 0 | $0.00 | $0.00 | $0.00 | $2.04 | 2020-02-14 | 2020-02-24 | 2020-02-24 | on order 2/14 | $0.00
A-0030 | M5-0.8 X 75MM Socket Head Cap Screws, Black Oxide Coated Steel | bolt depot | $0.44 | $0.12 | $0.05 | https://www.boltdepot.com/Product-Details.aspx?product=6534 | 1 |  | 4 | 2.42 |  | 4.00 |  | 4 | $2.42 |  | $0.00 | 0 | 0 | $0.00 | $0.00 | $0.00 | $2.42 | 2020-02-14 | 2020-02-24 | 2020-02-24 | on order 2/14 | $0.00
A-0031 | M6 Flat/Countersunk Head Socket Screws (M6 x 22mm) | bolt depot | $0.18 | $0.05 | $0.02 | https://www.boltdepot.com/Product-Details.aspx?product=13282 | 1 |  | 2 | 0.50 |  | 2.00 |  | 2 | $0.50 |  | $0.00 | 0 | 0 | $0.00 | $0.00 | $0.00 | $0.50 | 2020-02-14 | 2020-02-24 | 2020-02-24 | on order 2/14 | $0.00
A-0032 | M6-1.0 x 35mm Flat Head Socket Screws | bolt depot | $0.20 | $0.05 | $0.02 | https://www.boltdepot.com/Product-Details.aspx?product=13284 | 1 |  | 2 | 0.55 |  | 2.00 |  | 2 | $0.55 |  | $0.00 | 0 | 0 | $0.00 | $0.00 | $0.00 | $0.55 | 2020-02-14 | 2020-02-24 | 2020-02-24 | on order 2/14 | $0.00
A-0033 | M3-0.5x20mm Socket Head Cap Bolts Screws, 304 Stainless Steel 18-8, Allen Socket Drive, Fully Machine Thread, Bright Finish | bolt depot | $0.06 | $0.02 | $0.01 | https://www.boltdepot.com/Product-Details.aspx?product=13639 | 100 |  | 20 | 1.61 |  | 100.00 |  | 20 | $1.61 |  | $0.00 | 0 | 80 | $0.00 | $0.00 | $6.45 | $8.06 | 2020-02-14 | 2020-02-24 | 2020-02-24 | on order 2/14 | $0.00
A-0034 | M3 x 0.5mm 304 Stainless Steel Self-Lock Nylon Inserted Hex Lock Nuts, | bolt depot | $0.03 | $0.01 | $0.003624522922 | https://www.boltdepot.com/Product-Details.aspx?product=4792 | 100 |  | 46 | 2.02 |  | 100.00 |  | 46 | $2.02 |  | $0.00 | 0 | 54 | $0.00 | $0.00 | $2.37 | $4.39 | 2020-02-14 | 2020-02-24 | 2020-02-24 | on order 2/14 | $0.00
A-0035 | M3x6mmx0.5mm Stainless Steel Flat Washer | bolt depot | $0.01 | $0.002885720553 | $0.00124983549 | https://www.boltdepot.com/Product-Details.aspx?product=4513 | 100 |  | 46 | 0.70 |  | 100.00 |  | 46 | $0.70 |  | $0.00 | 0 | 54 | $0.00 | $0.00 | $0.82 | $1.51 | 2020-02-14 | 2020-02-24 | 2020-02-24 | on order 2/14 | $0.00
A-0036 | DIN 319 Ball Knob, .63" diameter, M4 threaded hole | jjwinco.com | $5.69 | $1.00 | $0.51 | https://www.jwwinco.com/en-us/products/1.1-Operating-with-handles-and-knobs/knobs/DIN-319-Steel-or-Aluminum-Ball-Knobs-with-Tapped-Hole-or-Blind-Bore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 | 1 | shipping estimated | 3 | 21.61 |  |  | 3.00 | 3 | $21.61 | 0 | $0.00 | 0 | 0 | $0.00 | $0.00 | $0.00 |  |  |  |  |  | $0.00
A-0037 | 1/4" thick Cast aluminum plate, 17" x 19" Cut from top plate waste) | midwest steel supply | $0.00 | $0.00 | $0.00 | https://www.midweststeelsupply.com/store/castaluminumplateatp5 | 1 | shipping estimated | 1 | 0.00 |  |  |  | 1 | $0.00 | 0 | $0.00 | 0 | -1 | $0.00 | $0.00 | $0.00 |  |  |  |  |  | $0.00
A-0038 | GT2x9 mm Kevlar-reinforced timing belt | reprapworld.com | $2.20 | $4.86 | $0.20 | https://reprapworld.com/products/mechanical/timing_belts/gt2x9_mm_kevlar_reinforced_timing_belt_per_meter/ | 1 | Outrageous shipping charge | 5 | 36.29 |  |  |  | 0 | $0.00 | 0 | $0.00 | 5 | 0 | $36.29 | $36.29 | $0.00 |  |  |  |  |  | $0.00
A-0039 | Polycarbonate sheet (Heat Saver 3-Wall) 10mm, 2' x 2' | Charleys grenhouse | $12.50 | $5.00 | $1.12 | http://www.charleysgreenhouse.com/B12900204-Heat-Saver-3-Wall-10mm---2--39-x-4--39.htm | 2 | Estimated shipping cost | 0 | 0.00 |  |  |  | 0 | $0.00 | 0 | $0.00 | 0 | 0 | $0.00 | $0.00 | $0.00 |  |  |  |  |  | $0.00
A-0040 | M4 x 0.7mm 304 Stainless Steel Nylon Lock Nuts | bolt depot | $0.04 | $0.01 | $0.004090370695 | https://www.boltdepot.com/Product-Details.aspx?product=4793 | 100 |  | 6 | 0.30 |  | 100.00 |  | 6 | $0.30 |  | $0.00 | 0 | 94 | $0.00 | $0.00 | $4.66 | $4.95 | 2020-02-14 | 2020-02-24 | 2020-02-24 | on order 2/14 | $0.00
A-0041 | M4x12mmx1 mm Stainless Steel Round Flat Washer | bolt depot | $0.01 | $0.003279227901 | $0.001420267603 | https://www.boltdepot.com/Product-Details.aspx?product=4514 | 100 |  | 30 | 0.52 |  | 100.00 |  | 30 | $0.52 |  | $0.00 | 0 | 70 | $0.00 | $0.00 | $1.20 | $1.72 | 2020-02-14 | 2020-02-24 | 2020-02-24 | on order 2/14 | $0.00
A-0042 | 2020 Series 3-Way End Corner Bracket Connector, with Screws | Amazon.com | $2.75 | $0.00 | $0.25 | https://www.amazon.com/PZRT-Connector-Standard-Aluminum-Extrusion/dp/B07BMQZZ2M | 4 |  | 0 | 0.00 |  |  |  | 0 | $0.00 | 0 | $0.00 | 0 | 0 | $0.00 | $0.00 | $0.00 |  |  |  |  |  | $0.00
A-0043 | HFS5-2020 aluminum extrusion, 553mm | misumi | $3.48 | $1.25 | $0.31 | https://us.misumi-ec.com/vona2/detail/110302683830/?ProductCode=HFS5-2020-200 | 1 | shipping estimated | 0 | 0.00 |  |  |  | 0 | $0.00 | 0 | $0.00 | 0 | 0 | $0.00 | $0.00 | $0.00 |  |  |  |  |  | $0.00
A-0044 | HFS5-2020 aluminum extrusion, 573mm | misumi | $3.60 | $1.25 | $0.32 | https://us.misumi-ec.com/vona2/detail/110302683830/?ProductCode=HFS5-2020-200 | 1 |  | 0 | 0.00 |  |  |  | 0 | $0.00 | 0 | $0.00 | 0 | 0 | $0.00 | $0.00 | $0.00 |  |  |  |  |  | $0.00
A-0045 | Aluminum angle 2.5" x 2.5" x .25" x 100mm | online metals | $4.08 | $1.00 | $0.37 | https://www.onlinemetals.com/en/buy/aluminum-angle | 3 | shipping estimated | 3 | 16.35 |  | 0.00 | 3.00 | 3 | $16.35 | 0 | $0.00 | 0 | 0 | $0.00 | $0.00 | $0.00 | $0.00 |  |  |  | mike donation | $0.00
A-0046 | HFS5-2020 aluminum extrusion, 200mm | misumi | $3.03 | $1.25 | $0.27 | https://us.misumi-ec.com/vona2/detail/110302683830/?ProductCode=HFS5-2020-200 | 1 | shipping estimated | 0 | 0.00 |  |  |  | 0 | $0.00 | 0 | $0.00 | 0 | 0 | $0.00 | $0.00 | $0.00 |  |  |  |  |  | $0.00
A-0047 | Lexan Sheet - Polycarbonate - .236" - 1/4" Thick, Clear, 24" x 12" | Amazon.com | $34.10 | $0.00 | $3.07 | https://www.amazon.com/Lexan-Sheet-Polycarbonate-Thick-Nominal/dp/B006JP5MXK | 2 |  | 0 | 0.00 |  |  |  | 0 | $0.00 | 0 | $0.00 | 0 | 0 | $0.00 | $0.00 | $0.00 |  |  |  |  |  | $0.00
A-0048 | Lexan Sheet - Polycarbonate - .236" - 1/4" Thick, Clear, 24" x 12" | Amazon.com | $17.05 | $0.00 | $1.53 | https://www.amazon.com/Lexan-Sheet-Polycarbonate-Thick-Nominal/dp/B006JP5MXK | 2 |  | 0 | 0.00 |  |  |  | 0 | $0.00 | 0 | $0.00 | 0 | 0 | $0.00 | $0.00 | $0.00 |  |  |  |  |  | $0.00
A-0049 | 350 X 350mm(Approx. 14" x 14"), 110V 800W, with 3M PSA & NTC 100K thermistor, KEENOVO Silicone Heater Mat/Pad, Huge Large 3D Printer HeatBed Build Plate Heater | Amazon.com | $69.99 | $0.00 | $6.30 | ebay (https://smile.amazon.com/approx-thermistor-KEENOVO-Silicone-Printer/dp/B011U919UO) | 1 |  | 1 | 76.29 |  | 1.00 |  | 1 | $76.29 | 0 | $0.00 | 0 | 0 | $0.00 | $0.00 | $0.00 | $76.29 | 2020-08-05 |  | 2020-08-17 |  | $0.00
A-0050 | Printer 3D Parts, FYSETC 12" x 12" x 0.3" 3D Printer Heated Bed Insulation Lightweight Foam Foil Self-Adhesive Insulation Mat | Amazon.com | $10.99 | $0.00 | $0.99 | https://www.amazon.com/FYSETC-Insulation-Lightweight-Self-Adhesive-Ultimaker/dp/B07DWPYQDS | 1 |  | 1 | 11.98 | x |  |  | 0 | $0.00 | 0 | $0.00 | 1 | 0 | $11.98 | $11.98 | $0.00 |  |  |  |  |  | $0.00
A-0051 | 350 x 350mm Flex Spring Steel Sheet Pre-Applied PEI | aliexpress | $43.37 | $0.00 | $3.90 | https://www.aliexpress.com/item/33058930261.html | 1 |  | 1 | 47.27 |  | 1.00 |  | 1 | $47.27 | 0 | $0.00 | 0 | 0 | $0.00 | $0.00 | $0.00 | $47.27 | 2020-08-05 |  | 2020-08-16 |  | $0.00
A-0052 | Redrex Dual Drive BMG Bowden Extruder High Performance Upgrading Parts (no motor) | Amazon.com | $23.99 | $0.00 | $2.16 | https://www.amazon.com/Redrex-Extruder-Performance-Upgrading-Geeetech/dp/B07QPWWYYK | 1 |  | 1 | 26.15 |  | 1.00 |  | 1 | $26.15 | 0 | $0.00 | 0 | 0 | $0.00 | $0.00 | $0.00 | $26.15 | 2020-08-05 |  | 2020-08-10 |  | $0.00
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

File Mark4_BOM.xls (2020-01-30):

Component / Sources | Purchase item | quantity | Price each | Shipping+Tax | Extended price | Subtotal | Actual | Comments
Top an bottom plate | aluminum plate 24"x48" | 1 | $80.00
Online metals | 0.375" Aluminum Plate 6061-T651 (Most common ) | 0 | $292.92 |  | $0.00
Howard Metals | Quote request sent to Howard Metals 11/28
ebay | https://www.ebay.com/itm/MIC-6-ALCA5-CAST-TOOLING-ALUMINUM-PLATE-3-8-x-24-x-24/261159881995 | 2 | $176.00 | $30.00 |  |  |  | Link from Mark. Mic6 for top and bottom?
midwest steel supply | https://www.midweststeelsupply.com/store/castaluminumplateatp5 | 2 | $112.00 | $61.00 | $285.00 |  |  | cast aluminum plate.
X and Y motors and standoffs | NEMA 17
amazon | STEPPERONLINE 0.9deg Nema 17 Stepper Motor Bipolar 2A 46Ncm/65oz.in 42x42x48mm 4-Wires DIY CNC | 2 | $21.50 | $3.78 | $46.78 |  | $45.70 | Purchased 12/3/19
amazon | uxcell 2Pcs 6063 Seamless Aluminum Round Straight Tubing Tube 1 Feet Length 0.156 Inches ID 0.39 Inches OD | 1 | $16.69 |  | $16.69 |  |  | need 4 pcs 29mm plus 4 pcs
X and Y motors and standoffs | NEMA 23
amazon | STEPPERONLINE 0.9 deg Nema 23 Step Motor Bipolar 1.26Nm(178.4oz.in) 2.8A 4-lead | 0 | $35.18 |  | $0.00 |  |  | https://www.amazon.com/STEPPERONLINE-Bipolar-1-26Nm-178-4oz-4-lead/dp/B07DV91Z2M
amazon | uxcell 6063 Aluminum Round Tube 300mm Length 12mm OD 5mm Inner Dia Seamless Aluminum Straight Tubing 1 Pcs | 0 | $8.09 |  | $0.00
Pulleys and idlers
amazon | Kee pang 10M Rubber Opening Belt 6mm Width+8pcs GT2 Pulley 20 Teeth Bore 5mm +4pcs Belt Locking Spring | 1 | $15.99 |  | $15.99 |  |  | 6mm belt
amazon | BALITENSEN Toothed GT2 Idler Pulley 20 Teeth 5mm Bore for 3D Printer 6mm Width Timing Belt (Pack of 5) | 0 | $7.90 |  | $0.00 |  |  | same price for this item to support 10MM belt
amazon | BIQU GT2 5mm Bore Aluminum Toothless Timing Belt Idler Pulley for 3D Printer 6mm Width Timing Belt (Pack of 5pcs) | 0 | $7.99 |  | $0.00
Amazon | 10 Pcs F688-ZZ (8165mm) Deep-groove Ball Bearings Rubber Sealed | 1 | $4.29 | $0.39 | $4.68 |  | $4.68 | Purchased 12/5/19 per Mark's suggestion
Amazon | GT2 10mm Idler Pulley 20 Teeth 5mm Bore (pack of 10) | 0 | $12.99 |  | $0.00 |  |  | Pack of 10
Amazon | Lots of bearing sizes at this path (see comments) |  |  |  |  |  |  | https://www.amazon.com/gp/product/B07NZ5PPHH
Idler axles
amazon | uxcell 6063 Aluminum Round Tube 300mm Length 12mm OD 8mm Inner Dia Seamless Aluminum Straight Tubing 2 Pcs | 1 | $8.14 |  | $8.14 |  |  | Cut to length for spacers to hold idlers are proper height.
amazon | uxcell 6063 Aluminum Round Tube 300mm Length 12.7mm OD 6mm Inner Dia Seamless Aluminum Straight Tubing 2 Pcs | 1 | $10.19 |  |  |  |  | https://www.amazon.com/uxcell-Aluminum-12-13mm-Seamless-Straight/dp/B07YKWJJGD
 | 8mm Cap screw, length = XX |  |  |  |  |  |  | Cap screw bolts.
Timing belt
reprapworld.com | GT2x9 mm Kevlar-reinforced timing belt | 5 | $6.40 |  | $32.00 |  |  | sold by the meter. 5M should give us extra.
Frame vertical corners | 80/20 Inc T-Slot 40mm x 80mm Aluminum Extrusion 40 Series 40-4080 x 750mm | 5 | $33.00 | $67.00
ebay | 80/20 Inc TSlot 40mm x 80mm Aluminum Extrusion 40 Series 40-4080-Lite x 1525mm (enough for 2)80/20 Inc TSlot 40mm x 80mm Aluminum Extrusion 40 Series 40-4080-Lite x 1525mm (enough for 2) | 0 | $56.89 | $75.00 | $0.00
Misumi | 4080 meduim duty (HFS8-4080-625) 625mm long | 4 | $22.68 | $19.24 | $109.96
Misumi | 4080 light duty (HFSL8-4080-625) 625mm long | 0 | $19.62 |  | $0.00
Misumi | 4080 high rigdity (GFS8-4080-625) 625mm long |  | $37.43 |  | $0.00
Plate to frame joining screws | 8mm flat head hex screws for frame | 10 | $6.00
amazon | Fullerkreg 18-8 Stainless Steel Hex Drive Flat Head Screw M8 x 1.25 mm Thread, 25 mm Long,Packs of 20 | 1 | $8.99 |  | $8.99
Exterior wall panels | double walled polycarbonate sheet | 1 | $24.00
Interstate Plastics | .630 X 24 X 48 CLEAR TWINWALL POLYCARBONATE | 2 | $32.00 |  | $64.00
Top cover walls | lexan 1/4" x 24x24 | 1 | $30.00
amazon | 24" x 24" x 1/4" Polycarbonate Clear Plastic Sheet LEXAN | 1 | $30.24 |  | $30.24
Top Cover walls | acylic 1/4" x 24x24 | 1 | $34.00 |  |  |  |  | Why not use polycarbonate here? - tougher and cheaper.
amazon | Acrylic Plexiglass Plastic Sheet 1/4" x 24" x 24" - Clear | 1 | $33.80 |  | $33.80
top enclosure framing | 20mm series extrusion for top enclosure | 1 | $70.00
amazon | 80/20 Inc, 20-2020, 20 Series 20mm x 20mm Extrusion x 1220mm (estimate needing 3 pcs) | 3 | $9.64 |  | $28.92 |  |  | 4 pcs @ 24 " + 4 pcs for posts @ 10"
top enclosure couplings | 20mm series 3 sided couplings | 8 | $3.00
amazon | 2020 Series Aluminum Profile Connector Set, 20pcs Corner Bracket,40pcs M5 x 10mm T-slot Nuts, 40pcs M5x10mm Hex Socket Cap Screw Bolt | 1 | $24.24 |  | $24.24
Front door hinges | hinges | 4 | $3.00 |  | $12.00
Print Bed | mic6 16"x16"x 1/4" for bed | 1 | $48.00 |  |  |  |  | Why not 6061 plate?
Online metals | 16 x 16 x.25 cast Aluminum plate | 0 | $141.88 |  | $0.00
Howard Metals | Quote request sent to Howard Metals 11/28 |  |  |  | $0.00
Midwest steel supply | 16 x 16 x.25 cast Aluminum plate | 1 | $45.90 | $11.96 | $57.86
Scrap | Use offcut from center of of the top plate. | 0 | $0.00 |  | $0.00 |  |  | Currently preferred solution.
Print bed frame | mic6 16"x16"x 3/8" for bed frame | 1 | $60.00 |  | $60.00 |  |  | Why is mic 6 needed for this?
Print bed heater
omega.com | Omega PN SRFGA-1212/5 12" x 12" silicone heater mat 120VAC, 720W up 20 232C | 1 | $88.00
omega.com | Omega PN SRmu01212-P 12" x 12" silicone heater mat 120VAC, 360W up 20 232C | 1 | $71.24
amazon | 300 X 300mm (Approx. 12" X 12") 120V 750W, KEENOVO Universal Flexible Silicone Heater Mat/Pad, 3D Printer Heated Bed Heating Element | 1
amazon | Wisamic 310x310mm 120V 750W Silicone Rubber Heater with 3M Tape, Screw Holes for 3D Printer CR-10 CR-10S S3 | 1 | $39.99 |  | $39.99
Print bed bottom insulation | ceramic fiber blanket insulation for bed | 1 | $20.00
amazon | Printer 3D Parts, FYSETC 12" x 12" x 0.3" 3D Printer Heated Bed Insulation Lightweight Foam Foil Self-Adhesive Insulation Mat Sticker Hotbed Thermal Pad for CR-10 Reprap Ultimaker Makerbot - 2 Pack | 1 | $10.99 |  | $10.99
Enclosure rear wall | Garolite sheet 24" x 24" x 1/4" sheet for electronics mount 8525K134 | 1 | $24.00
Mcmaster carr | Economical Electrical-Insulating Garolite Sheet 1/4" 24x24 | 1 | $40.93 |  | $40.93
Build plate surface | 16" PEI sheet .065" | 1 | $27.00 |  | $27.00 |  |  | Not needed if we use magnetic build plates
Bridge | Aluminum 24" x1.5" x .375" |  |  |  |  |  |  | Mike's guess ate the size.
online metals | 0.375" x 1.5" Aluminum Rectangle Bar 6061-T6511-Extruded | 1 | $9.04 |  | $9.04
Extruder | Dual material, dual gear drive.
Bondtech | Bondtech BMG-X2 (Mark's recommendation, dual material, dual gear) Includes stepper | 1 | $135.00 |  | $135.00
Bondtech | Bondtech BMG Extruder (single material) |  | $80.00 |  | $0.00
Amazon | SINGLE - Redrex Dual Drive BMG Bowden Extruder High Performance Upgrading Parts (no motor) |  | $22.99 |  | $0.00
amazon | Usongshine Nema 17 Stepper Motor (For use with stepper-;ess extruder) |  | $8.89 |  | $0.00
 | triangle labs double geared extruder |  | $60.00 |  | $0.00 |  |  | From Mark's spreadsheet. Can't finsd on Amazon
Hot end
filastruder | The Mosquito Hotend | 0 | $144.99 |  | $0.00
aliexpress | Mosquito clone | 2 | $53.00 |  | $106.00 |  |  | https://www.aliexpress.com/item/4000088018308.html
Hot end frame
 | 1/8"x 4x6" aluminum sheet metal for hot end frame | 0 | $5.00 |  | $0.00
online metals | 1/8 thick T6061 sheet 4" x 6" | 1 | $3.97 |  | $3.97
 |  |  |  |  | $0.00
Y-axis linear rails | TEN-HIGH linear rail, 1pcs CNC Parts MR12 MGW12 Miniature Linear Guide Rail Way Slide 500mm | 2 | $77.00
amazon.com | TEN-HIGH linear rail, 1pcs CNC Parts MR12 MGN12 Miniature Linear Guide Rail Way Slide 500mm+2pcs MGN12C Slider Miniature Linear Motion Guide Way | 2 | $65.10
banggood | Machifit 500mm Length MGN15 Linear Rail Guide with MGN15H Linear Rail Block CNC Tool | 2 | $25.91 | $15.80 | $67.62 |  | $67.62 | Purchased 12/1/19
X-Axis linear rail | TEN-HIGH Linear Rail, 2pcs CNC Parts MR12 MGN12 Miniature Linear Guide Rail Way Slide 500mm
banggood | MGN12 500mm Linear Rail Guide with MGN12H Block CNC Tool | 1 | $21.59 |  | $21.59
Amazon | ReliaBot 500mm MGN12 Linear Rail Guide with MGN12H Carriage Block
Z-Axis ball screw | SFU1204 500mm Ballscrew kit | 1 | $60.00
Amazon.com | SFU1204 500mm Ballscrew kit + Set BK/BF10 Kit + 1204 Ballscrew RM1204 L500mm Ball Screw with Ball Nuts + Screw Nut Housing for CNC Machine | 1 | $56.00 |  | $56.00
ebay | FUYU CNC Linear Slide Motion Rail Stage G1610 Ball Screw Guide Actuator Table (400mm) | 1 | $225.92 |  |  |  |  | Also Eliminates the need for the 2 Z-Axis linear rails,Z-axis motor, extra carraiges (~$ 151)
Z-Axis shaft coupling | 8mm shaft coupling
amazon.com | Sydien 2 Pcs 8mm to 8mm Motor Shaft Coupling Aluminum Alloy Flexible Stepper Motor Coupler | 1 | $7.99 |  | $7.99
Z-Axis linear rail | 500mm linear rail - wide
amazon.com | ReliaBot 500mm MGN15 Linear Rail Guide with MGN15H Carriage Block | 2 | $45.99 |  | $91.98
Extra carraige block for Z-Axis linear motor
amazon.com | MGN15 Linear Rail Guide Block, MGN15H Mini Linear Motion Guide Rail Slider Bearing Steel Sliding Block | 2 | $13.88 |  | $27.76
Z-axis motor NEMA 23 | NEMA 23 stepper for Z-Axis
amazon.com | Nema 23 Stepper Motor 2.8A 1.9Nm (269oz.in) 76mm Length with 8mm Diameter of Shaft | 1 | $23.99 |  | $23.99
Controller board | Duet 2 clone
Donation from Mark | Duet 2 32 bit motion control board clone | 1 | $0.00 |  | $0.00
amazon | Duet 2 32 bit motion control board clone |  | $83.00 |  | $0.00
User interface | Paneldu 7" touchscreen
filastruder | paneldu i5 7" touch screen | 1 | $99.99 |  | $99.99
Wire
 | wire | 1 | $20.00 |  | $20.00
Power supply
amazon | EAGWELL 24v 15a DC Universal Regulated Switching Power Supply 360w | 1 | $24.68 |  | $24.68
SSR for mains voltage heated bed | SSR for mains voltage heated bed | 1 | $20.00
amazon | Ogrmar SSR-25 DA 25A 3-32V DC / 24-380V AC Solid State Relay and Heat Sink | 1 | $10.99 |  | $10.99
Connectors
 | connectors | 1 | $20.00 |  | $20.00
 | Total build cost |  |  |  | $1684.80 |  | $118.00 |  | $0.00

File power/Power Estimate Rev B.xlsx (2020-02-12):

Part # | Description | Source/Part Number | Voltage | Current (Amps)* | Power (Watts) | Note
 | Controller
A-0056 | Duet WiFi Motion Controller Board | Duet3D/Duet 2 Wifi Motion Controller Board, v1.04 | 5 VDC | 0.3 | 1.5
No P/N | PanelDue Color Touch Screen Controller | Duet3D/PanelDue | 5 VDC | 0.7 | 3.5
A-0056 | Duex5 Expansion Board | Duet3D/Duex 5X
 | Bed Heater
A-0049 | Silicone Heated Mat (120 VAC, 750 Watts) | Wisamic Silicone Rubber Heated Mat/H010029 | 120 VAC | 6.25 | 750 | Thermister Controlled
 | Stepper Motors for X,Y,Z(1,2,3) motion:
A-008 | X Stepper (NEMA 23) | Stepperonline/23HM22-28045 | 24 VDC | 1.02 | 24.5 | Max Duet WiFi output current is 2.4A
A-008 | Y Stepper (NEMA 23) | Stepperonline/23HM22-28045 | 24 VDC | 1.02 | 24.5 | Max Duet WiFi output current is 2.4A
A-019 | Z Stepper #1 (NEMA 17) | OSM Technology Company/17HM19-16845 | 24 VDC | 0.68 | 16.3
A-019 | Z Stepper #2 (NEMA 17) | OSM Technology Company/17HM19-16845 | 24 VDC | 0.68 | 16.3 | Expansion Board
A-019 | Z Stepper #3 (NEMA 17) | OSM Technology Company/17HM19-16845 | 24 VDC | 0.68 | 16.3 | Expansion Board
 | Planetary Steppers for Extruder Tool Lock/Unlock
No P/N | Tool Stepper #1 (NEMA 11) | OSM Technology Company/11HS12-0956D | 24 VDC | 0.37 | 8.8 | Not Energized During Print Ops (Reqs Duex 5X)
 | Extruder Tool Powered Components
A-0053 | Extruder Filament Drive Motor #1 ( E0) | Usongshine NEMA 17 Stepper Motor 1.8 Deg/17H54023 | 24 VDC | 0.6 | 14.4
A-0053 | Extruder Filament Drive Motor #2 (E1) | Usongshine NEMA 17 Stepper Motor 1.8 Deg/17H54023 | 24 VDC | 0.6 | 14.4 | Alternately Energized
No P/N | Heater Cartridge #1 (E0) | E3D/E-Heater-24-30W | 24 VDC | 1.25 | 30
No P/N | Heater Cartridge #2 (E1) | E3D/E-Heater-24-30W | 24 VDC | 1.25 | 30
No P/N | HotEnd Fan #1 | FYSETC/US-Ender 3 4010 Brushless Fan 24 V | 24 VDC | 0.1 | 2.4
No P/N | HotEnd Fan #2 | FYSETC/US-Ender 3 4010 Brushless Fan 24 V | 24 VDC | 0.1 | 2.4
No P/N | Part Fan #1 | Filastruder/Generic 4020 Ball Bearing 24 VDC Part-Cooling Blower Fan | 24 VDC | 0.1 | 2.4
No P/N | Part Fan #2 | Filastruder/Generic 4020 Ball Bearing 24 VDC Part-Cooling Blower Fan | 24 VDC | 0.1 | 2.4 | Alternately Energized
 | 5 VDC Total |  |  | 1 | 5
 | 24 VDC Totals |  |  | 7.48 | 179.5
 | 5 and 24 VDC Power Total (Determines Rated Power of 24 VDC PS) |  |  |  | 184.5 | 24 VDC Power Supply Must Be Rated >Than This
 | 120 VAC Totals |  |  | 6.25 | 750
 | Total Input Power |  |  |  | 934.5
 | AC Input Current |  |  | 7.79
 | 24 VDC Power Supply
A-057 | 24v 15a DC 360 Watt Universal Regulated Switching Power Supply (85% Eff) | EAGWELL/LED0060S360W24V15A
 | Yellow Highlight indicates load during print operation counted in power total
 | * Using Calculated Stepper Current IAW: Isc = (Vmot / Vps)*C* Iph*M
 | Isc = Stepper Power Supply Load Current
 | Vmot = Stepper Phase Voltage
 | Vps = Power Supply Voltage
 | C = Number of Coils (Usually 2)
 | Iph = Stepper Phase Current
 | M = Margin of Safety (Use 1.75)

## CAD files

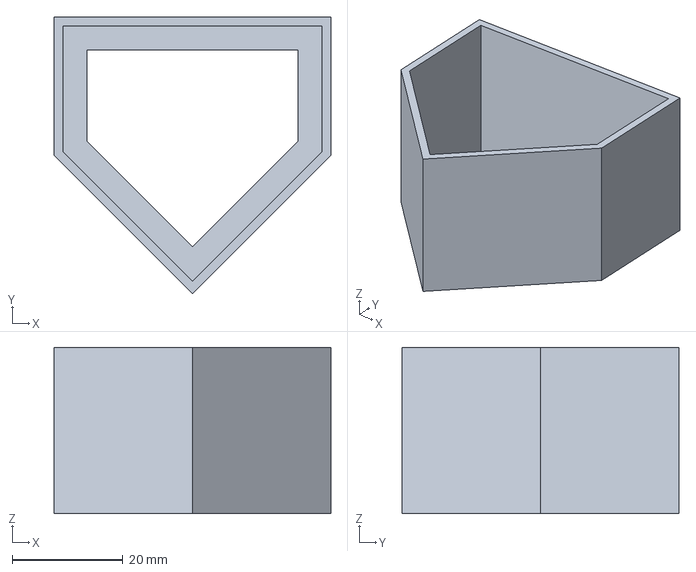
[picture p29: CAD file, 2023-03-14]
gcode_Duet_2/test patterns/PA test part.3mf
50.0 x 50.0 x 30.0 mm

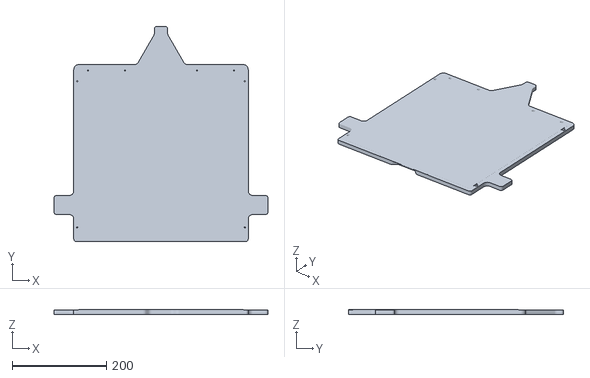
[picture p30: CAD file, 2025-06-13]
slicer ini files/TechLab/Mark4_Bed.stl
453.7 x 456.0 x 9.82

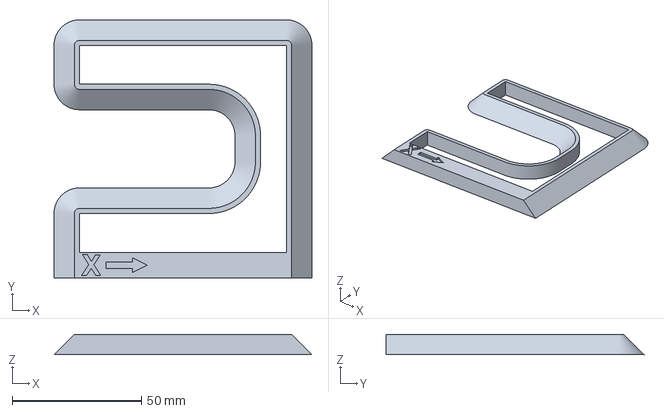
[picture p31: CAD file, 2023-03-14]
gcode_Duet_2/test patterns/serpentine.3mf
99.8 x 99.9 x 7.89 mm

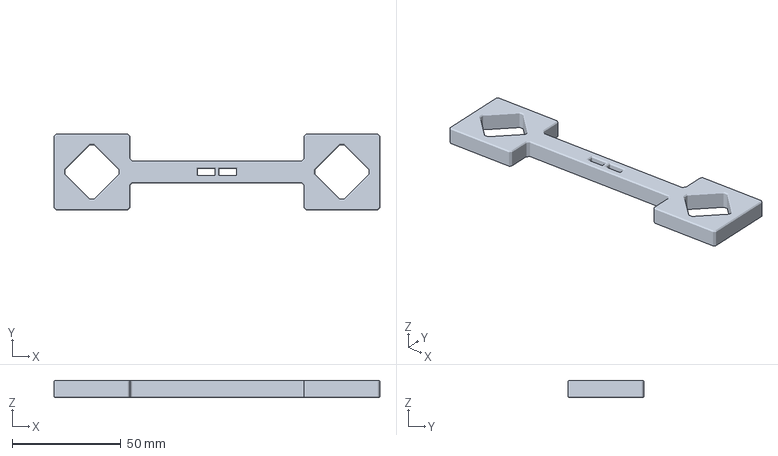
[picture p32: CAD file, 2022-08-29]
gcode_Duet_2/test patterns/dimensional analysis test part.3mf
150.0 x 35.0 x 8.00 mm

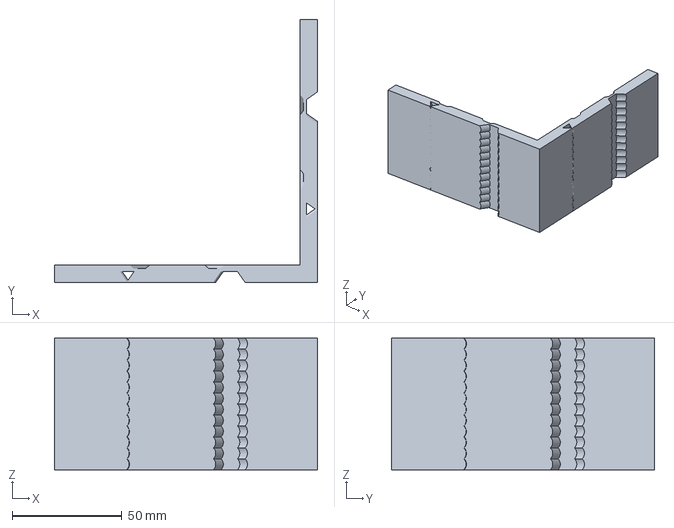
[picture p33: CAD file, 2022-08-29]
gcode_Duet_2/test patterns/ringing_tower.3mf
120.0 x 120.0 x 60.0 mm

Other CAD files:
Fusion360_model/2020 v1.f3d
Fusion360_model/4080 v1.f3d
Fusion360_model/Duet WIfi Rev 4 v1.f3d
Fusion360_model/Mark3_corexy_belt_mount.f3d
Fusion360_model/Mark3_new_z_vertical_bracket.f3d
Fusion360_model/Mark3_new_z_vertical_bracket_front.f3d
Fusion360_model/Mark3_z _back_bracket_final.f3d
Fusion360_model/mark3_new_z_vertical_bracket_sides(2).f3d
Fusion360_model_NEW/jubilee carriage back plate CBP-05 mods v3.f3d

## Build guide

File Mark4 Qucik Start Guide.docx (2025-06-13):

Mark4 Printer

Quick Start Guide

(For more details see the user guide in the binder)

# PrusaSlicer

Select the Mark 4 printer | - In the Printer Settings Tab in PrusaSlicer, pull down the printer list and select the Mark4 from the Physical Printers near the bottom of the list.
First Layer height | - Should be .2mm or greater
Speeds | - Speeds up to 100mm/sec should produce good prints. Printer capped at 150mm/sec.
Save on SD card | - Same as you do with the Prusa printers.

# Running the Mark4 Printer

Clean the build Plate | - Windex has been working best – dry with a paper towel.
Power on | - Switch on the back left corner of the Mark4, just below the power cord.
Watch the Z probe | - The BLTouch probe drops twice and, turns red at power-on.
Prep the printer | - Follow the on-screen instructions.
Load your filaments | - Select a tool by touching that tool's icon on the touch-screen. - Touch the macro button on the screen, follow the prompts. - Thread you filament through the plastic tube when loading
Start your print job | - Put your card in the SD slot on the right side of the touch screen housing. - Touch this button on the control screen: - Touch it again on the next screen to get to the card you inserted. - Select your file, then the print button.
Watch Layer 1 | - Adjust baby steps if necessary (It should not be needed) to move the nozzle closer or farther from the bed. The pictures on the buttons tell you which way it'll move – the bed closer to nozzle or nozzle closer to the bed.
Finishing up | - Remove the build plate from the printer and take off your parts. - Unload your filament. - Turn off the printer at the power switch.

Mark 4 Printer BETA Phase rules

1. If something goes wrong – shut off the printer (power switch and unplug). Add a note to the log.
2. If everything goes right – note your usage in the log – date, time, your name, filament type.
3. If you're not sure, consult the User Guide in the binder in the drawer. If you're still not sure, ask a monitor. If they are not sure, leave a note or send a message in SLACK (eta-large-3d-printer channel).
4. You must be able to use slicer to adjust temperatures, layers, speeds. (If you are a complete beginner, it might be best to start with the Prusa printers)

# 5. If your print fails or something odd happens, we want to know so we can correct it. Leave a note or send a message in SLACK.

6. Weekly maintenance, repairs, and improvements happen Tuesday between 10am and 2pm. We'll try not to, but may stop a running print during this time window.

BARN TechLab Mark4 Qucik Start Guide.docx Version 1.0 Page 2/2

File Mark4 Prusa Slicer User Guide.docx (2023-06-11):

Mark4 PrusaSlicer

User Guide

# Overview

Slicing operations in PrusaSlicer are mostly the same as for other Tech Lab 3D printers, once the Mark4 Printer has been selected. This section only discusses slicing options that are important for using the Mark4.

Other slicers may be able to generate acceptable gcode for the Mark4 printer, but we have only created a printer profile for PrusaSlicer because it's the slicer most used in the Tech Lab.

This version of the user guide is written around the current (as of June 2023), single extruder version of the printer. If we are successful in implementing a tool changer for this printer, major changes in the process will be needed.

# Select the Mark4 printer

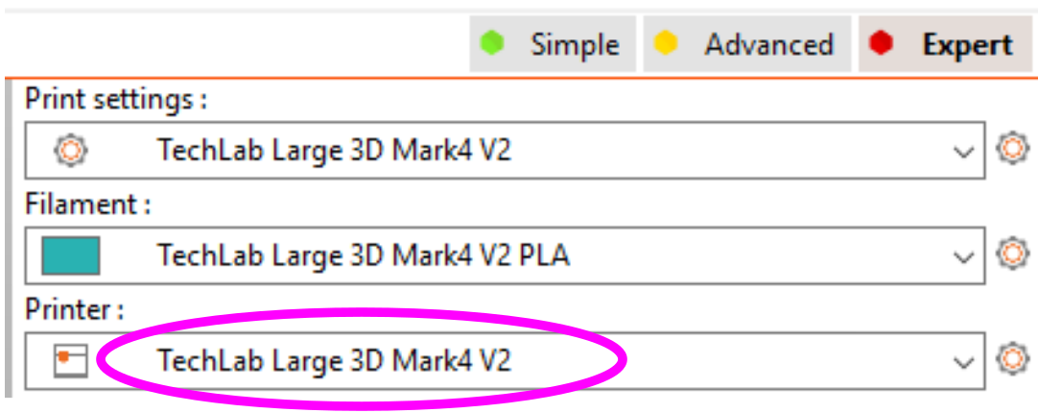
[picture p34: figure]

1 | In the Plater or Printer Settings Tab, pull down the printer list and select "TechLab Large 3D Mark4 V2" from the Physical Printers near the bottom of the list. In the future, if we update the printer profile, you may find V3 (or later) instead of V2. You should not need to make changes to any of the settings for the Mark4. If you think there are some needed, please talk to the Mark4 team.

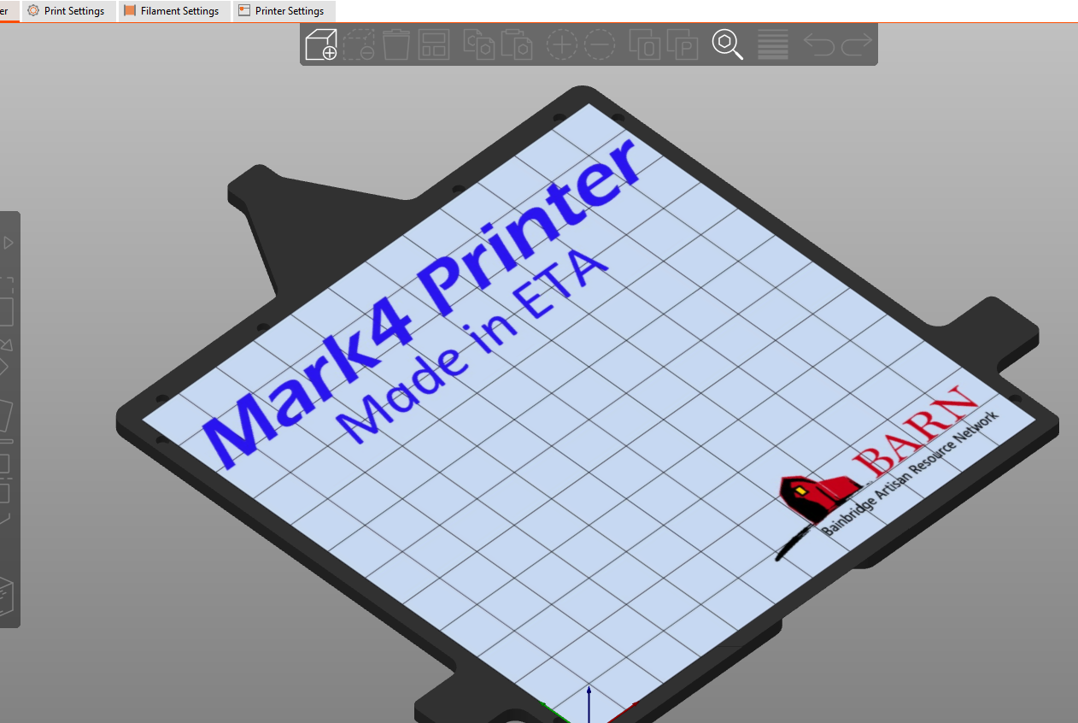
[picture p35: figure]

2 | The Plater Tab should show the shape of the Mark4's bed and the printable area of the build plate.

# Filament Settings

In general, the Mark4 should use filament settings similar to the Prusa printers in the Tech Lab.

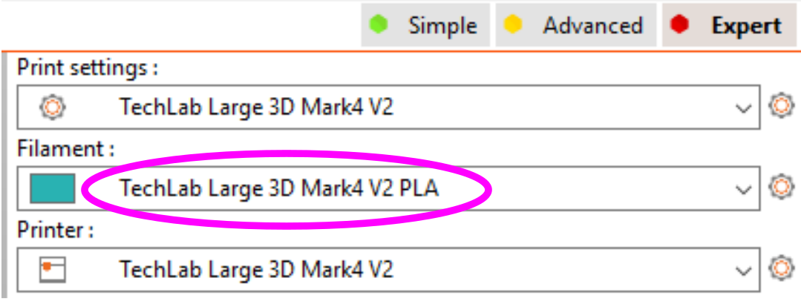
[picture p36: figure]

1 | In the drop down menu in the Plater or Filament Settings Tab, select one of the filaments starting with "TechLab Large 3D Mark4 V2".
2 | At present we only have a filament setting for PLA, but we plan to add more soon. In the meantime, you can create a new user preset for other types. | First Layer Other Layers Material Bed Nozzle Bed Nozzle PLA 60 215 60 215 PETG 68 225 65 225 TPU ?? ??

# Print Settings

In general, the Mark4 should use print settings similar to the Prusa printers in the Tech Lab. We'll only list the parameters with "strong" recommendations here.

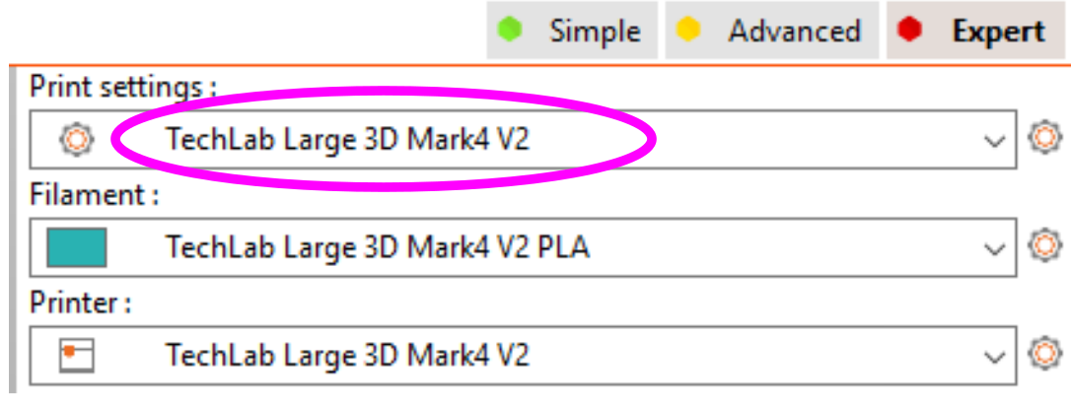
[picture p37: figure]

1 | In the drop down menu in the Plater or Print Settings Tab, select one of the filaments starting with "TechLab Large 3D Mark4 V2". Are you spotting the naming trend?
2 | Layers and Perimeters (Print Settings Tab) Note: First Layer heights below 0.2mm are not recommended, to avoid possible damage to the plastic surface of the build plate. | Layer Height 0.2mm * First Layer height 0.2mm * Layer heights as low as .1mm are achievable for finely detailed prints.
3 | Speed (Print Settings Tab) The Mark 4 is faster than the Prusa printers because the bed does not move and toss your part around. Expect to use higher speeds for faster print jobs. Note: As we continue to test and tune the Mark4, we will try to increase the speed limits. | Quality parts can be achieved with Print speeds of 100mm/s and higher. The machine speed limit is 150mm/s
4 | Acceleration control (advanced) - don’t mess with it. | The printer configuration should have blocked user changes to acceleration. Do not unblock this.
5 | Pressure Equalization (experimental) – don’t mess with it. | The printer's firmware has pressure equalization settings for most common filament types. No need to use this setting

# Export your gcode file

1 | Save your gcode file to an SD card and head to the printer.

BARN TechLab Mark4 Prusa Slicer User Guide Version 1.0 Page 1/2

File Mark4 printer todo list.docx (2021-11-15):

Mark4 printer todo list – As of 11/1/2021

1. ~~Fab A~~~~luminum top plate and print bed.~~ Done
2. Fab heated bed. Done
  a. ~~Define magnet holes – locations and depths.~~ Done. 36 pockets that can handle a magnet up to .5" diameter, and cut to a depth to leave 2mm of aluminum between the magnet and the top of the heated bed.
  b. Define spring fastenings or other keepers are each kinematic ball location. Done. Threaded hole for spring near each kinematic seat.
  c. ~~Mounting features for heater cable and thermistor cable.~~ Done.
  d. ~~Define redundant thermal overrun protection (thermistor location and any required grooves for cable).~~ Done. Thermal cutoff switch mounting added. Need to select cutout temperature.
  e. ~~Build final print-bed side of bed kinematic supports.~~ Done
3. Prep heated bed.
  a. ~~Install kinematic seats on bottom of bed plate.~~
  b. Test 3/8" SmCo magnets.
    i. ~~Make 36~~ ~~13.5mm diameter disks, ~4mm thick to user as spacers below the magnets.~~ ~~Done. Made 3.2mm thick.~~ Done
    ii. ~~Place one magnet in the bottom of each hole, followed by a spacer and a piece of blue tape.~~
    iii. ~~Test hold of steel build plate~~. Done
    iv. Decide if we need to switch to ½" diameter magnets. – 3/8" magnets seems good enough.
    v. After step 4b(ii): Blue-tape bed heater to bottom of bed and plan wiring for thermal cutoff and bed heater.
    vi. Decide whether or not to use a cable chain to manage the power and thermistor wires going to the bed heater.
    vii. Buy aluminum spacers from sendcutsend to replace the wood plugs. ~~Done~~. May add 1mm laser cut Delrin spacer on that.
    viii. ~~Buy ½" magnets if needed.~~ Done. Not needed.
    ix. Assemble heated bed with magnets, aluminum spacers, and really using the adhesive of the heater. No turning back after this.
4. Replace wood top plate with Aluminum.
  a. Before stripping anything down:
    i. ~~Run bed leveling and bed mesh~~ ~~compensation~~ ~~measurement on the wood heated bed.~~ ~~and~~ ~~save the resulting file. This is to use as a baseline for future measurements.~~ Done
    ii. ~~Put the aluminum heated bed on and repeat bed leveling and mesh compensation measurement.~~ Done
  b. Transfer process.
    i. ~~Remove belt from prototype.~~ Done
    ii. ~~Remove~~ ~~pulleys~~ ~~and standoffs, making sure to provide stops to prevent the Y rails from running off their tracks.~~ Done
    iii. ~~Lubricate all pulley ball bearings with WD40 and ensure they are spinning freely. Clean any grease and accumulated crud from the surface the belt rides on.~~ Done.
    iv. ~~Assemble pulleys on al~~~~uminum top plate using the new~~ ~~aluminum standoffs.~~ Done
    v. ~~Remove bridge from y rails~~. Done
    vi. Remove, clean, and replace the ball bearing pulleys on the bridge. Mostly done. Need to clean pulleys of accumulated grease and gunk.
    vii. ~~Remove carriage from bridge and carefully remove the sliding block from the rail. It might be easiest to remove the rail from the bridge.~~ Done
    viii. Check that all ball bearings are in the sliding block and replace it on the rail. Check that the block slides freely on the rail. Reinstall the rail on the bridge if it was removed. Be sure to put keepers on the rail to prevent the block from sliding off.
    ix. Remove the Y rails and check their bearings the same way the X rail was checked. Note that the ball bearings for the Y rail are larger than those for the X rail Do not use X rail balls in the Y rails.
    x. Install the Y rails on the new top plate with approx every third screw. Tighten only the screws on the left side rail. Install the stop-blocks on behind the Y rails using locktite on the screws.
    xi. Install the bridge between the rails, using a framing square to ensure the X and left Y rails are perpendicular. Before tightening the screws.
    xii. Use the rail and Y blocks as a spacer to get the right Y rail perfectly aligned before tightening the screws in the right Y rail. The bridge should slide easily with no sticky spots. It might be necessary to loosen the screws on the left Y rail to get things "perfect".
    xiii. ~~Remove the Motors and any remaining HW from the wood proto top plate.~~ Done
    xiv. ~~Remove the wood top plate and replace it with the aluminum top plate.~~ Done
    xv. ~~Install the motors and other hardware.~~ Done
    xvi. One by one, remove the screws holding the bride to the Y blocks and reinsert using locktite.
    xvii. Recheck the spacing on the Y rails. If it's good, add remaining screws using locktite, then recheck the spacing and make adjustments if necessary. Remove the initial screws and reinsert them using locktite.
    xviii. Install the carriage on the bridge, using locktite on the screws.
    xix. Install the belts. Be sure to use the new aluminum belt keepers.
    xx. Tension the belt.
    xxi. Power up and run some tests.
5. Cable management concept from dock to tool. Be sure to enable multiple docked tools and one mounted tool.
  a. Define /prototype tool parking concept. Done. Parking plates designed. Need to cut and thread parking posts.
  b. Finalize cable management structure (rainbow material) that can reach to all corners of the build plate when attached to the tool, and not interfere with others on tools that are docked.
  c. Decide how cables get from controller to dock-end of cable management structure. Maybe holes through the top plate near each tool dock. Done. Cables route over the rear edge of the top plate. A 2020 extrusion is screwed to the bottom to provide a mounting point for the end of the rainbow.
6. Define Cable management concept from control board to dock
  a. Define control board mounting. Replace prototype plywood board with "something", ideally cuttable on Big Red. Options:
    i. FR4 (aka garolite) – not lasercuttable? But maybe can be marked with the laser for hole locations?
    ii. Acrylic – not ideal because it might get too warm and is brittle.
    iii. Aluminum sheet?
  b. Be sure to add standoffs between boards and the board.
  c. Define interface connection for all cables
7. Fab aluminum bottom plate
  a. Get some nylon footed leveling feet for the base.
  b. Do we really need the base plate to be made from aluminum? What does Al do for us that the current MDF does not?
8. Complete enclosure design
9. Document setup and calibration procedures
  a. HW assembly, particularly Z-axis components.
  b. Belt tensioning procedure
  c. Define and create any needed HW setup gages.
  d. As-built documentation
  e. SW parameters – z-offsets, dive-heights, other user parameters in the gcode file
10. Optimize Z-axis limit switch mount HW and location
  a. Move home switch position to top of Z axis. Will require combining this function into the z-probe.
  b. Need to prove the inductive switch will work with an aluminum plate so.
  c. Can we also put in a safety limit switch on the bottom of the rail to work as a backup to prevent over-lowering?
11. Investigate wobble and squeak of Z-Axis acme shafts – they wobble and make noise.
  a. Is there enough force to wobble the build pate?
  b. Add Nylon bearing to top end of shaft.
  c. Can we straighten out any slight bends.
  d. Replace one Z-Axis shaft coupler that failed. Maybe switch to a more flexible coupler.
  e. Redrill motor mount holes on Z axis motors to allow some motor movement.
  f. Investigate swapping R/L brackets that hold the Ball side of the Kinematic mounts. Might allow moving the rails and motors up so motors cam be installed without removing the base plate. 6/9 – Investigation complete – decided not to pursue. Moving motor mounts up 12mm will make it so we can get the motors out. Of their mounts without the need to remove base plate.
12. Define the tool lock/unlock motor assembly
  a. Buy parts to allow duplication of the Jubilee lock morot – tensioning cable, springs, limit switches, etc. ,
  b. Motor position
  c. Acquire/print/assembly parts
13. Build a "real Jubilee" tool using the mosquito hot end we bought for the project. Done
  a. Current tool is prototype.
  b. Water cooled print head ala Mark McComsey – NOT YET.
14. Add an "estop" switch on the printer for user immediate shutoff.
  a. Pick an unused IO port on the duet. See GCode M581 for setting up a trigger. https://duet3d.dozuki.com/Wiki/M581
15. Decide on "production" use model for printing and maintenance
  a. If Panel Du, acquire one and figure out where it attaches to the machine
  b. If web-control, need to figure out the controller (Rpi zero?), plus keyboard, mouse, etc.
  c. Our Duet board is wireless. We need to get the wireless in the studio to be robust, rework the Duet board to become wired, or replace the Duet with a wired-LAN version.
16. Before reassembly
  a. Verify all rail blocks have a full complement of bearings
  b. Make alignment tools for assembly (laser cuttable when possible)
    i. Z motor mounts – z direction.
    ii. Z- side rail #1 – perpendicular to top plate and centered on 4080 slot.
    iii. Z-side rail #2 – parallel to rail #1 (link blocks together)
    iv. S-back rail – perpendicular to top plate.
    v. Zrails vertical
    vi. Y rails- parallel to each other (link blocks together with bridge)
17. After assembly with the new top and bottom plates, and heated bed
  a. Complete alignment of print bed/ nozzle/ probe.
18. Add LED lights and camera?
19. Additional sw work
  a. Define, inherit macro for tool docking
  b. Z-axis homing – move down or up?
  c. Investigate Duet "input shaping" (M593) to reduce/eliminate ghosting at higher speeds. https://duet3d.dozuki.com/Wiki/Input_shaping
  d. Investigate Duet "Pressure Advance" https://duet3d.dozuki.com/Wiki/Pressure_advance

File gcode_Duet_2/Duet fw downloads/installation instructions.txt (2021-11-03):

If you are updating update from something older than 3.0, you MUST UPDATE TO 3.0 FIRST.

Copy the file "Duet2 and 3Firmware-3.0.zip" the sys directory on the SD card using the web interface. The system should ask if you want to install the new fw. Say yes.

If you are already at 3.0 or higher, you should follow the same procedure for teh latest fw zip package.

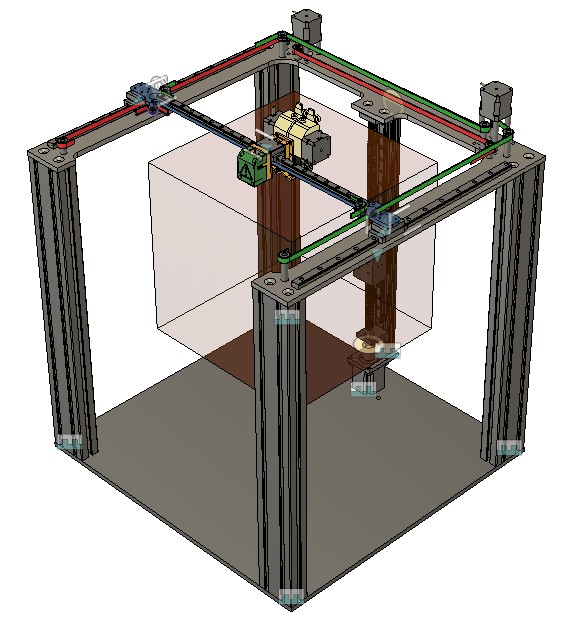
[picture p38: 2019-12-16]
Fusion360_model/images/assembly_v45.jpg

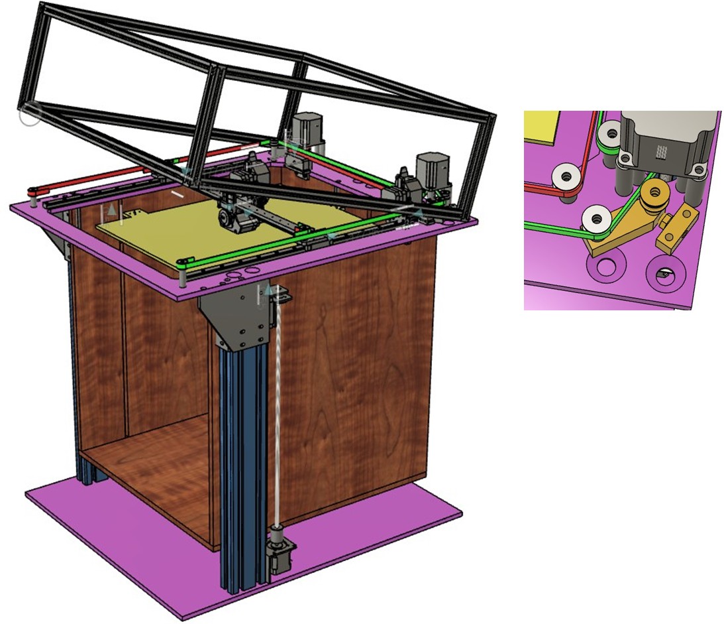
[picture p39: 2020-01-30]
Fusion360_model_NEW/images/New_assembly_2020_01_30.jpg

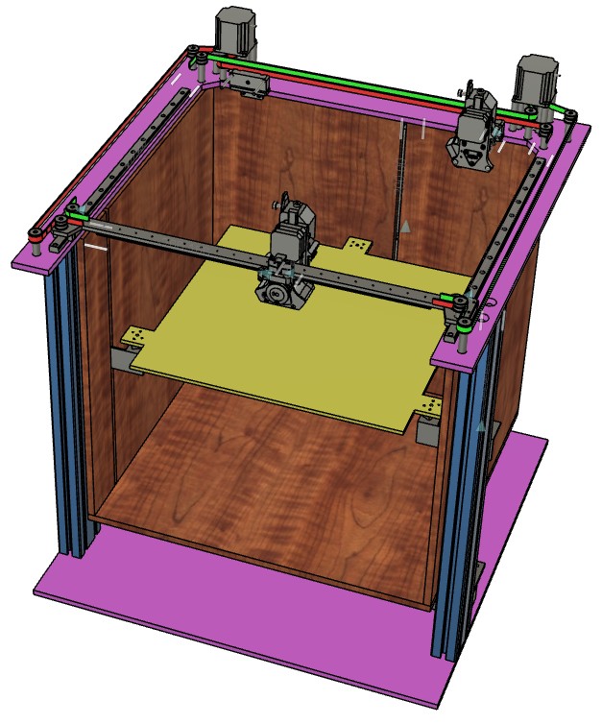
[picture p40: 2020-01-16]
Fusion360_model_NEW/images/New_assembly_2020_01_16.jpg

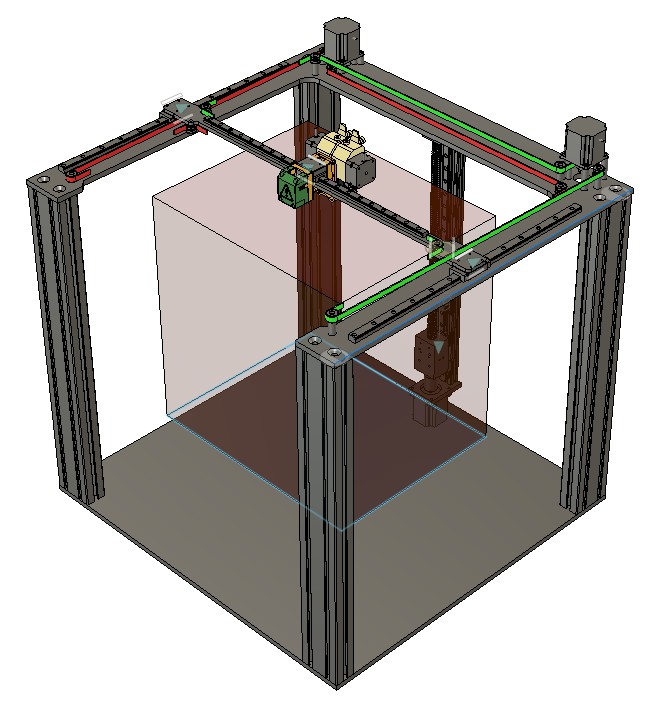
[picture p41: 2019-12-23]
Fusion360_model/images/New_Assembly_V10.jpg

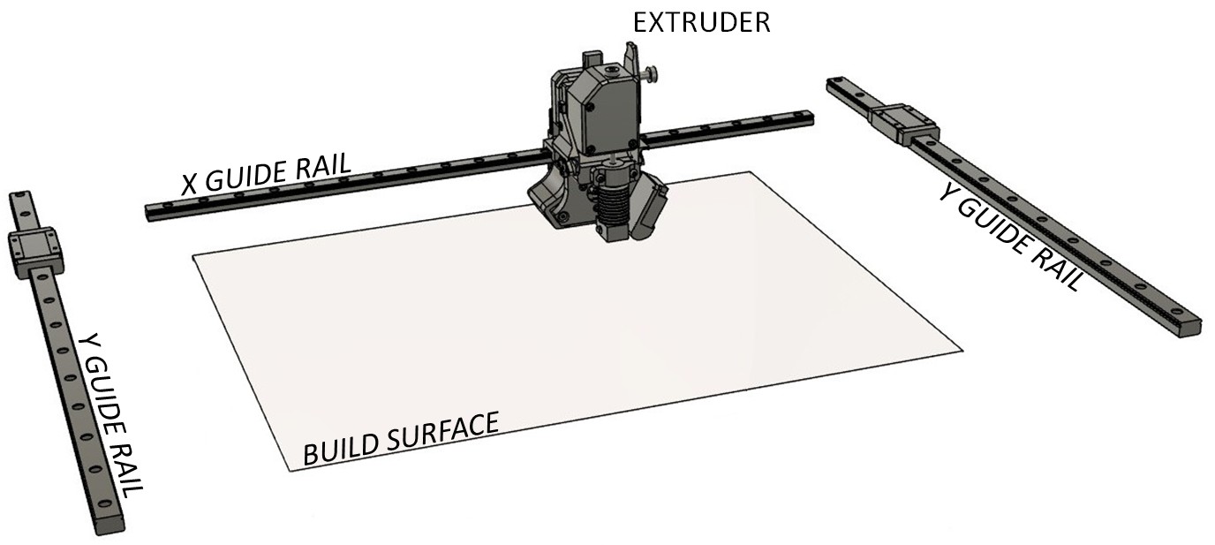
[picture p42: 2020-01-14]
images/generic_xy_guides.jpg

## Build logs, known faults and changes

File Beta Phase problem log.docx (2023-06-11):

PROBLEM LOG - BETA

TechLab Large 3D Printer – Mark4

During the Beta phase of the printer, users should log all problems they have.

Date | User name | Problem description

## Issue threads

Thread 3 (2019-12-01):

BOM should include total cost, including shipping and tax

wabmester, 2019-12-01:
I looked at one of the "sure things" in the BOM -- 4080 extrusions.    Shipping added $81 to the cost.    Some items will have "free shipping" which just means the shipping cost is factored in, so for those items without free shipping, we need to include shipping in the cost estimate.    Same with sales tax -- it all comes out of the same budget.

wabmester, 2019-12-04:
Add column for shipping cost.

Closed 2019-12-04.

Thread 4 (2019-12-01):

BOM: need clarification on rails

wabmester, 2019-12-01:
Looks like 2 x 400mm MGN12 rails got replaced by 1 x 400mm MGN15.

Need clarification on quantity and width.

Also, is it correct that we want 500mm for Y and 400mm for X?

wabmester, 2019-12-04:
Replaced by 3 x MGN15 rails.

Closed 2019-12-04.

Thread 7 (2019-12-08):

Y-Rail in BOM is 400mm. Should it be 500mm?

mikeabuilder, 2019-12-08:

mikeabuilder, 2019-12-08:
The bridge part provided by Mark looks to be designed for a 500 mm rail. Our BOM has a 400mm X-Rail.  If we keep the 400mm rail, we'll need to move the mounting holes on the bridge.

mikeabuilder, 2019-12-08:
Maybe the bridge part is too wide. When I added the main coreXY plate to the CAD model, that's what it looks like.

wabmester, 2019-12-10:
See https://github.com/BainbridgeArtisanResourceNetwork/Mark4_printer/issues/4

There was an error when transcribing Mark's BOM.    That's why I ordered 500mm rails for both X and Y.

mikeabuilder, 2019-12-11:
Just added the "build volume" to the Fusion model, and I can verify that we need 500mm rails in the Y direction in order to support a 350mm Y part size and also have additional travel available for a tool changer. I'll update the BOM, and I'm closing this issue,

Closed 2019-12-11.

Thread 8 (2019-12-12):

X-axis rail: MGN 15H we purchased too wide for Mark's bridge.

mikeabuilder, 2019-12-12:
The pulley spacing on Mark's bridge is too close to support a 15mm rail. I've switched to an MGN 12H rail in the Fusion model. We already bought a pair of 15mm rails, which we can use on the Y-axis. I'll update the BOM to make the X rail 12mm.

wabmester, 2019-12-12:
Recall the discussion about MGN12H vs MGN12C.    Verify that we don't want the smaller slide.

mikeabuilder, 2019-12-12:
12H block is about 10mm longer (in direction of travel) than the 12C, and the H is rated for much higher torque (about 150% of the C). There is a spec table in the materials folder (https://github.com/BainbridgeArtisanResourceNetwork/Mark4_printer/blob/master/Materials/linear_rail_X_axis/Similar_part_different_supplier_use%20MGN15H.jpg)  Both C and H are the same width. If the 10mm makes a difference, I'll be surprised. In any case, no purchasing until we like the Fusion design, so we'll see a problem if the "H" block is too big.

wabmester, 2019-12-12:
Jubilee went with 12C on X because it was sufficient to handle torsional load and gave a smaller footprint.    Looks like the 12H sticks out a bit in your design.    I'm sure either works fine.

mikeabuilder, 2020-03-09:
Currently running a 12C block on the proto (thanks for the loaner Doug) and have a 12C on order. When we finalize the carriage design, we will have both blocks in hand and can choose the one we like best. Closing this issue

Closed 2020-03-09.

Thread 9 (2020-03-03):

Z slides can slide off rails

wabmester, 2020-03-03:
There is a stop at the top of the Z rails, but there's a gap between the bottom of the rail and the motor bracket.   The slide (and ball bearings) can move into this gap.

mikeabuilder, 2020-03-04:
At the top, we can the aluminum retainer is less than 3mm above the end of the rail. we can drop it down to touch (or nearly touch) the end of the rail. On the bottom, we can design a printed plastic part that connects to the 4080 aluminum with a T-nut and prevents the carriage from sliding off the end.  We can also create a place to fasten a microswitch that can be used as the Z-Max end stop.

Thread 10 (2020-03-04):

WOOD BRIDGE - allowing Belt B standoffs to tilt.

mikeabuilder, 2020-03-04:
The plywood bridge is being crushed when tension is applied to the B Belt, allowing the standoff to tilt so much that the belt is running off the pulley when the carriage moves in the X-direction.

3/3 - Two ideas for addressing. Idea 1 - Build an aluminum bridge, if we can put both the "new and old" standoff locations. Idea  2 - Make small end-pieces for the bridge where the pullets are fastened and hook it to the wooden bridge (in some manner).  Challenge with both is getting it fabbed quickly. #2 may be able to be hand-built. #1 needs to be coordinated with the metal shop.

mikeabuilder, 2020-03-09:
I have created a temporary bridge that we can use until we get an aluminum proto manufactured.  I followed idea #2 above.

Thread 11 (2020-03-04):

Bridge and carraige do not have working X-endstop switch locations.

mikeabuilder, 2020-03-04:
Need to add design features to the bridge and also the carriage to hold the selected end-stop switch and give it a place to engage the mechanism.

mikeabuilder, 2020-03-09:
Created a new part to hold a specific micro-switch carrier to the holes in the Jubilee carriage.  Also adjusted the Bridge to have a flat surface opposite the switch so there is a good surface for it to act on. Will keep open until it is shown to work on the proto.

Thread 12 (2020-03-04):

WOOD PROTO - Frame racking

mikeabuilder, 2020-03-04:
With the wood proto, it is easy to rack the frame by pushing on the side. We won't know if this is an issue in the final product until we make the aluminum top and bottom plates.

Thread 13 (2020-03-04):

WOOD PROTO - Belt attachment to carraige not working (in many ways)

mikeabuilder, 2020-03-04:
Multiple issues:

1. No mechanism to easily connect the belt,  Currently, both ends are fastened at the same time.
2. No mechanism to ensure the belt is attached at the correct Z-height.
3. The 3mm screws are too tiny. Too hard to get a wrench on them.
4. It would be good to fit a belt tensioner to the belt fastening.

More?

mikeabuilder, 2020-03-09:
A new, temporary design has been added to the Fusion Model. This design has 5 pieces, a main piece and 4 wedges (one wedge for each belt end). Each belt end is attached separately, and all belt ends can be attached to the main body without attaching the body to the Jubilee carriage.  This should be good-enough for the wood proto.  Will leave this open until the parts are assembled on the proto and shown to work as intended.

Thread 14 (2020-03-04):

WOOD PROTO Belt tensioners can't add enough tension

mikeabuilder, 2020-03-04:
In their current configuration, the belt tensioners cannot move the belt enough to increase the tension in the way we'd like. Not how much the flexing of the top plate is adding to this issue. Also not sure if stretching of the proto rubber belt is contributing to the issue in a way that the final kevar belt would not.

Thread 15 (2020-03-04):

need location to mount electronics

wabmester, 2020-03-04:
Where will the power supply and Duet board mount?    Would be nice to include that in the model.

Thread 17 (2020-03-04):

too much torque on pulleys?

wabmester, 2020-03-04:
I was really struck by how tall the pulley stand-offs were (due to the 9mm belts) and how much torque they were getting (sufficient to torque the MDF top quite a bit).

Time to consider adding supports?   See the Jubilee design for a nice approach.

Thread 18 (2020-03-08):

Mounting holes for kinematic bed attach on Z-axis brackets do not line up with posts on the supports.

mikeabuilder, 2020-03-08:
The posts on the "ball on a post" half of the heated bed kinematic connector do not line up with the holes on the brackets that extend out from the Z-Axis rails. They need to align.

mikeabuilder, 2020-03-09:
Thanks for finding this Clayton.  It's an error.  The holes in the bracket were moved ~ 2mm.

Closed 2020-03-09.

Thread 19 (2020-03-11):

image in README.md is of old mark3 design.

theOGbaber, 2020-03-11:

mikeabuilder, 2020-11-16:
Hi Clayton,

Hope this message reaches you, and hope you are staying safe. We've missed you in the large 3D printer meetings since we got back into the studio in October. That lasted less than 2 months. We're back on virtual meetings as of this week, and expect to continue this way at least until mid-December, but I think probably much longer.

Progress on the printer has been slow, but Ralph has been making great progress on the electronics. He's got all the motors hooked up and is able to move the carriage around. Also move the bed up and down.  We've got a new prototype where the belts connect to the carriage. Still needs work, but it has an arrangement that equalizes the tensions in both belts and the tightening is done with the tuning machine from a ukulele. Kind of goofy looking, but it seems to work.

Anyway, hope things are good in your world and hope to see you back at BARN some day.

Mike

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

Closed 2020-11-16.

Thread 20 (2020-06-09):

Z-axis motor mount screw holes too big

mikeabuilder, 2020-06-09:
The screw holes for the motor on the Z-Axis motor mount are 5.5mm diameter, and the screws for these holes are M3. Need to reduce the hole size to 3mm dia.

mikeabuilder, 2020-06-09:
Model updated to reduce the hole size to 3mm. I also shortened the "other leg" of the motor mount by 5mm to make it fit better into the raw material I have for machining.

Closed 2020-06-09.

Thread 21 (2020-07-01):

Current heated bed design exceeds agreed upon max part dimension of 350mm

mikeabuilder, 2020-07-01:
The present design file has a build plate that enables parts that are 41.5mm bigger in the Y direction that the specified 350mm.  The frame is also 41.5mm bigger than necessary in the same direction.  The agreed max part size is 350 x 350.

mikeabuilder, 2020-07-01:
I propose changing the build plate size to match the agreed dimension, but leave the frame at it's current dimension. Reason for leaving the frame at the present size is that it allows us 42.5mm of "play" in precisely where we locate the build plate in the Y dimension. We have not finalized the tool changer and it's parking and may want to adjust the build plat location some.

mikeabuilder, 2020-07-23:
After team discussion, the heated bed Y dimension has been reduced to 365mm. This is 350mm for the build plate, plus 15 mm at the back end for build plate alignment pins and threaded holes that may be used in the future to extend the heated bed into the area under the tool parking space.  The rear edge "thermal isolation slots" have been removed and the whole of the space in the rear had been removed, except for a cantilevered section that reaches to the rear kinematic joint. The attached picture shows the new shape.
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

Closed 2020-07-23.

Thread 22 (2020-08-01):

Looks like the Jubilee carraige might not fit our bridge.

mikeabuilder, 2020-08-01:
One design goal for the Mark 4 is to be able to use the Jubilee carriage if we want. There are a few things that look like they might not be compatible. Need to verify the latest Jubilee design will work.

1. Position of the belts (x, y, and z directions) relative to the fastener on the Jubilee carriage.  May need to change the pulley positions on the bridge, and/or the pulley standoff heights.
2. Alignment of the mounting holes to the X-Rail block. Jubilee uses a "C" style (Compact) block.
3. X-endstop "target". The latest Jubilee design uses an extension of the standoff for the "high pulley" on the front of the left side of the bridge as a place for the X-endstop microswitch to hit. Our current design has the "low pulley" at the front so there is no standoff to extend into the endstop target. May need to swap high and low pulleys in our design.

See picture. Jubilee in back, Mark design (in progress) in front.
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

mikeabuilder, 2020-08-05:
I've done a close comparison of the Jubilee carriage design already in our Fusion model (the "OLD" jubilee carriage) and the latest that was posted to Jubilee's github.  I've attached a pdf of the comparison of the major parts, but the conclusion is that although there are some changes in the new Jubilee carriage design, the major interfaces (Carriage to X-axis sliding block, Carriage mounting plate to tool, and carriage back plate to belts) nave not changed. This meanss no changes to pulley locations are needed.  I have swapped the "high" and "low" pulley positions in our model. The A belt is not the higher belt and the B belt is lower. This will allow us to build an x-Axis microswitch target into one of the belt standoffs, like the Jubilee.
[OLDER ve NEWER Jubilee Carriage.pdf](https://github.com/BainbridgeArtisanResourceNetwork/Mark4_printer/files/5031563/OLDER.ve.NEWER.Jubilee.Carriage.pdf)

mikeabuilder, 2020-08-13:
Closing this issue. The team reviewed and approved the changes to the model:

1. Swapped high and low standoffs to match the Jubilee arrangement.

Closed 2020-08-13.

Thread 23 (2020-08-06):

Heated Bed Y alignment under new Jubilee carriage is broken

mikeabuilder, 2020-08-06:
With the new Jubilee Carriage and tool docks inserted into the drawing, the 350mm Y dimension of the heated bed is too far towards the rear of the frame. The current heated bed is 365mm from rear edge to front edge.  The first image below shows the closest approach of the Jubilee extruder tool on the carriage to an identical docked tool leaves the extruder nozzle  ~43mm from the edge of the heated plate.  This is the Y = 0 position. The second image shows the extruder in the Y= 350mm position.  In this position, the extruder is off the front of the heated bed by ~28mm. There is also a near-collision between the bridge and the B Belt pulley .

Proposed solution is

1. Move the rear and front edges of the heated bed forward by 30mm.
2. Cut back the bridge in the area of the near-collision.
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

mikeabuilder, 2020-08-13:
I've updated the Fusion model, moving both the front edge and the rear edge of the heated bed forward by 30mm. The pictures below show the new minY and maxY carriage positions, and a second tool docked. If the team approves this change, I'll close this issue.
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

Closed 2020-08-13.

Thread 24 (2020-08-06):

Jubilee Carriage Belt attach mechanism too low (z direction) for our pulley placement by 2.2mm

mikeabuilder, 2020-08-06:
I've updated the master design file with the latest Jubilee carriage and tool changer parts. The image below shows that the belts hit the carriage back plate too high in the Z-direction. The distance is approx 2.2mm.  The shortest standoff on the bridge pulleys is 0.9mm, so we cannot move the belts down without reducing the thickness of the bridge in that area.  The bridge is currently 6.35mm thick. Need an analysis of what minimum material removal would be needed to accommodate. We could also change the carriage center to make the adjustment but would violate the goal of being Jubilee carriage compliant.  The team needs to make a decision on this.
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

mikeabuilder, 2020-08-06:
Forgot to note that the Y-direction alignment of the bridge pulleys and the carriage rear plate is off my 0.2mm as this closeup shows. Note that the teeth are not drawn on the belt, so the interference see in the green belt is expected. It should be 1.0mm and it is 1.2mm.
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

mikeabuilder, 2020-08-08:
Moved the pulleys on the bridge my 0.2mm to eliminate the Y-direction alignment error reported in the last comment.

mikeabuilder, 2020-08-13:
The team discussed the options in the 8/11/2020 meeting and agreed that we should make changes to the Jubilee "back plate" design on the carriage to accommodate our 9mm belts. This means enlarging the space where the the  belts attach, and moving up the top belt clasp so it is centered on our belt. Mike will make a new Fusion file to make and document these changes.

mikeabuilder, 2020-08-13:
The Jubilee carriage backplate has been modified to accommodate the Mark 4 wider belts. The fusion model for this is in the repo in this location: https://github.com/BainbridgeArtisanResourceNetwork/Mark4_printer/blob/master/Fusion360_model_NEW/jubilee%20carriage%20back%20plate%20CBP-05%20mods%20v3.f3d. If a team review does not recommend additional changes, this issue will be closed.

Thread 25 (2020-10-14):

Kinematic supports look hard to manufacture

mikeabuilder, 2020-10-14:
The current design of the "linear guide" side of the kinematic joints for the heated bed rely on machining a V-grove in a small piece of steel. Manufacturing this might be difficult. I made another design that uses an alimunim block and two press-fit 4mm steel rods as the "linear guide" surface. In order to mate to the existing mounting holes for this part, and have the mounting screws not hot the steel rods, I needed to increase the thickness of the fixed block and we'll need to tap blind holes. I made the part wider so I could add more holes that don't require blind tapping and allow for a thinner fixed block - but do require new holes in the bed. We can decide which path (short and wide vs tall and narrow) before we lock the design of the heated bed. Old and new designs are shown below.
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

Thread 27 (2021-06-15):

WOOD PROTO - Y-rail placement prevents full docking

mikeabuilder, 2021-06-15:
The Y rail placement on the second wood top plate does not allow the tool to fully engage the tool dock before the sliding block comes to the end of the rail. The rail needs to move rearwards by ~12mm. The picture shows the gap between the tool bracket (brown plastic part) and the plate on the tools dock (plywood) when the block is at the end of the rail.
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

mikeabuilder, 2021-06-15:
I'll drill a new set of holes for the Y rails and move them rearwards 12mm. I'll also update the fusion design to reflect this change.

mikeabuilder, 2021-06-16:
I modified the wood top plate to move the Y-rails rearward by 12mm. Now the tool can move into the docking area without having the block fly off the rail. The two pictures show the block and rail at Y-max and Y-min positions. Next step is changing the design in Fusion.

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

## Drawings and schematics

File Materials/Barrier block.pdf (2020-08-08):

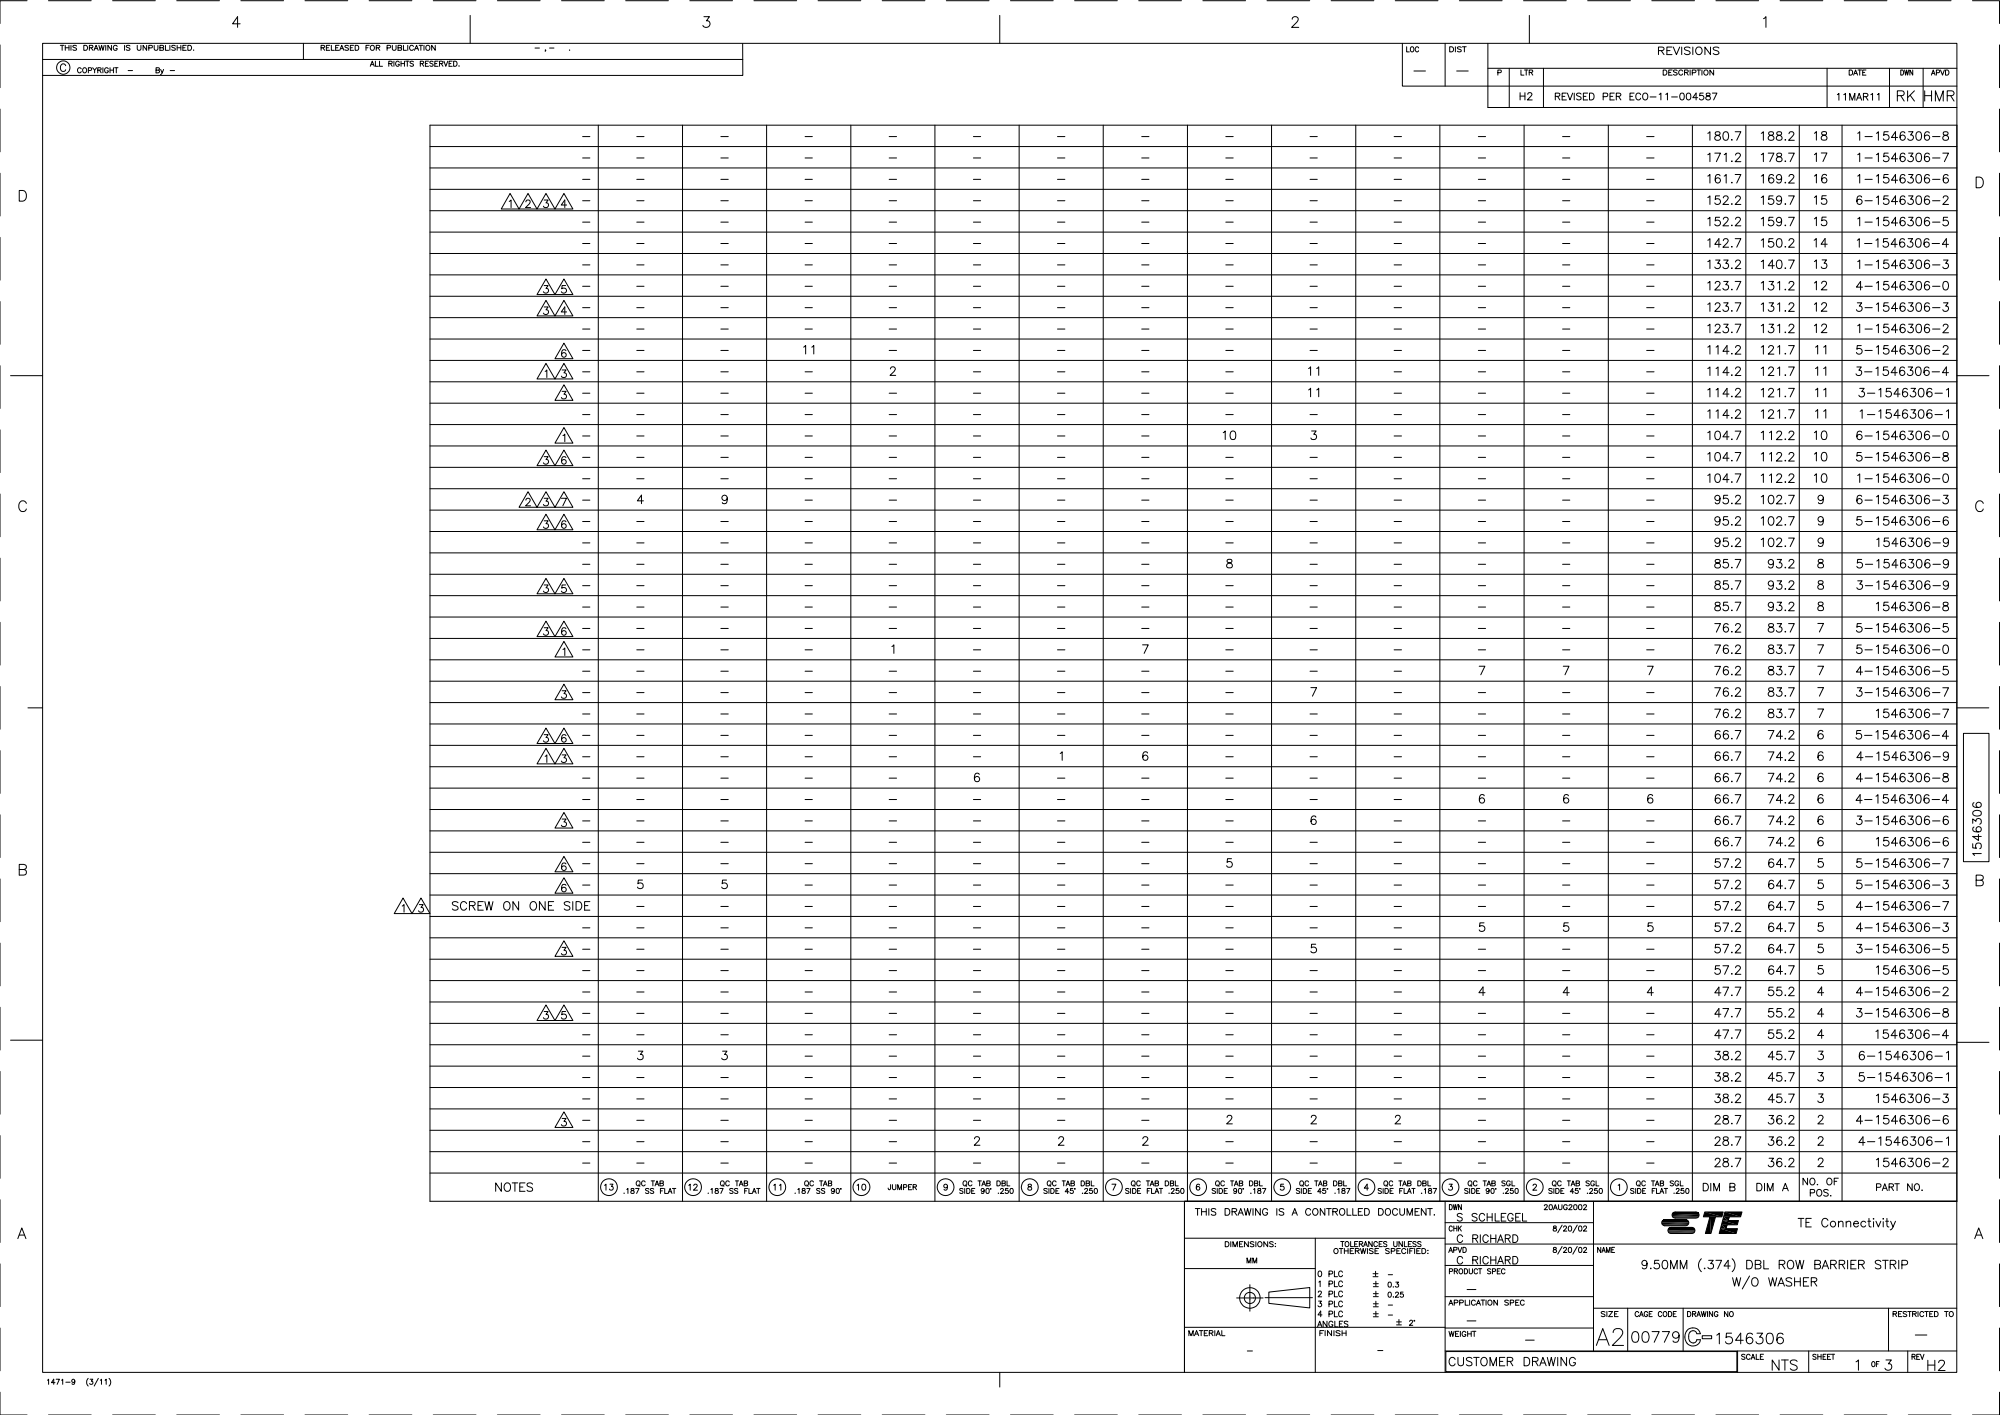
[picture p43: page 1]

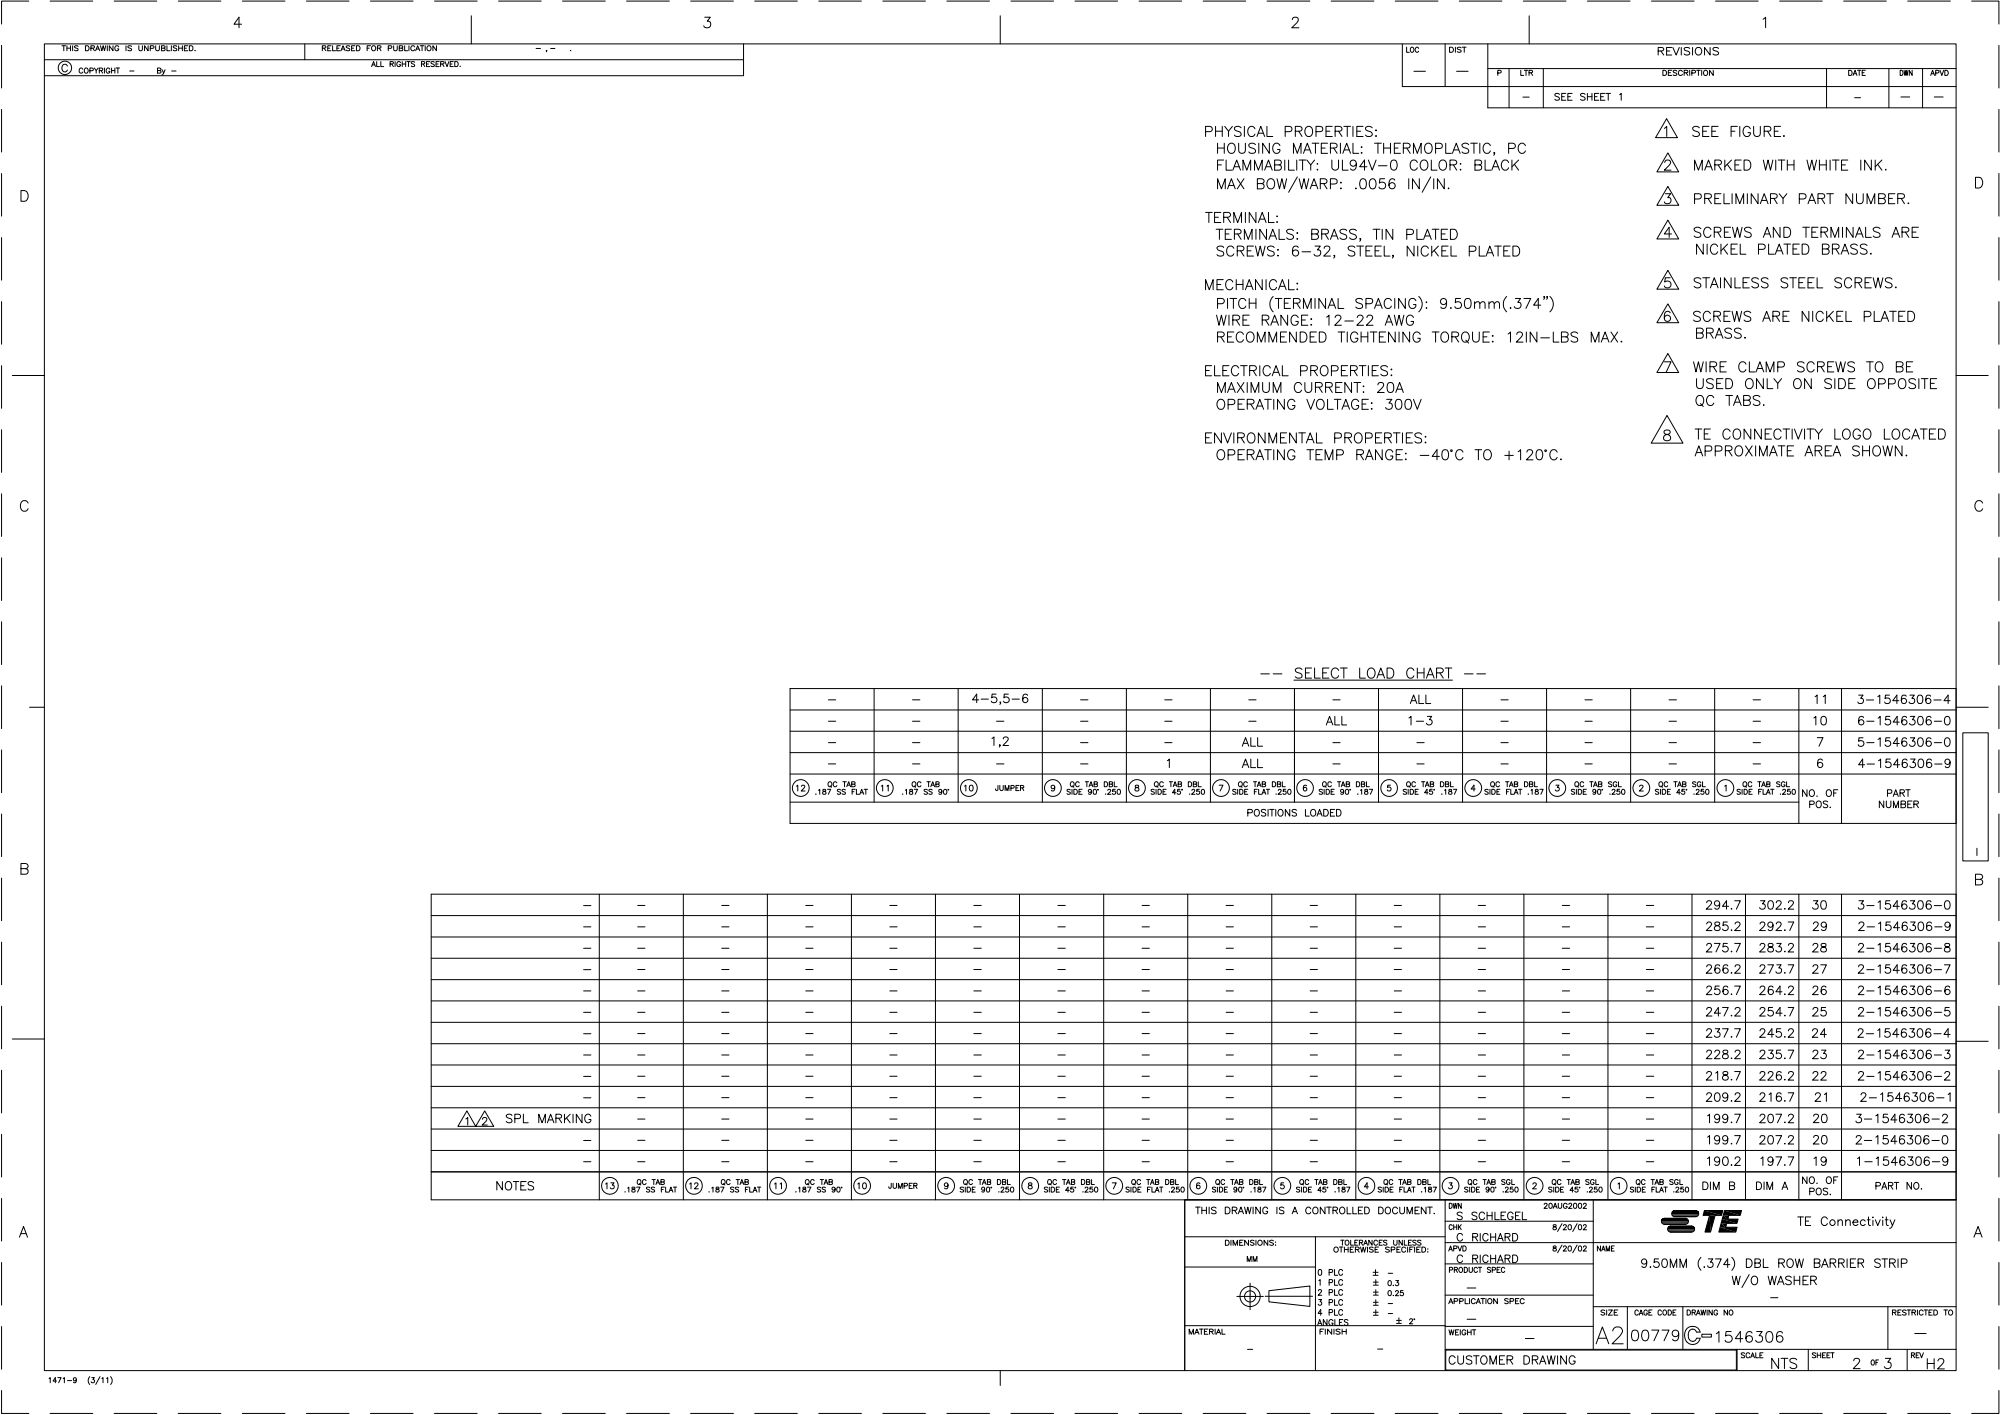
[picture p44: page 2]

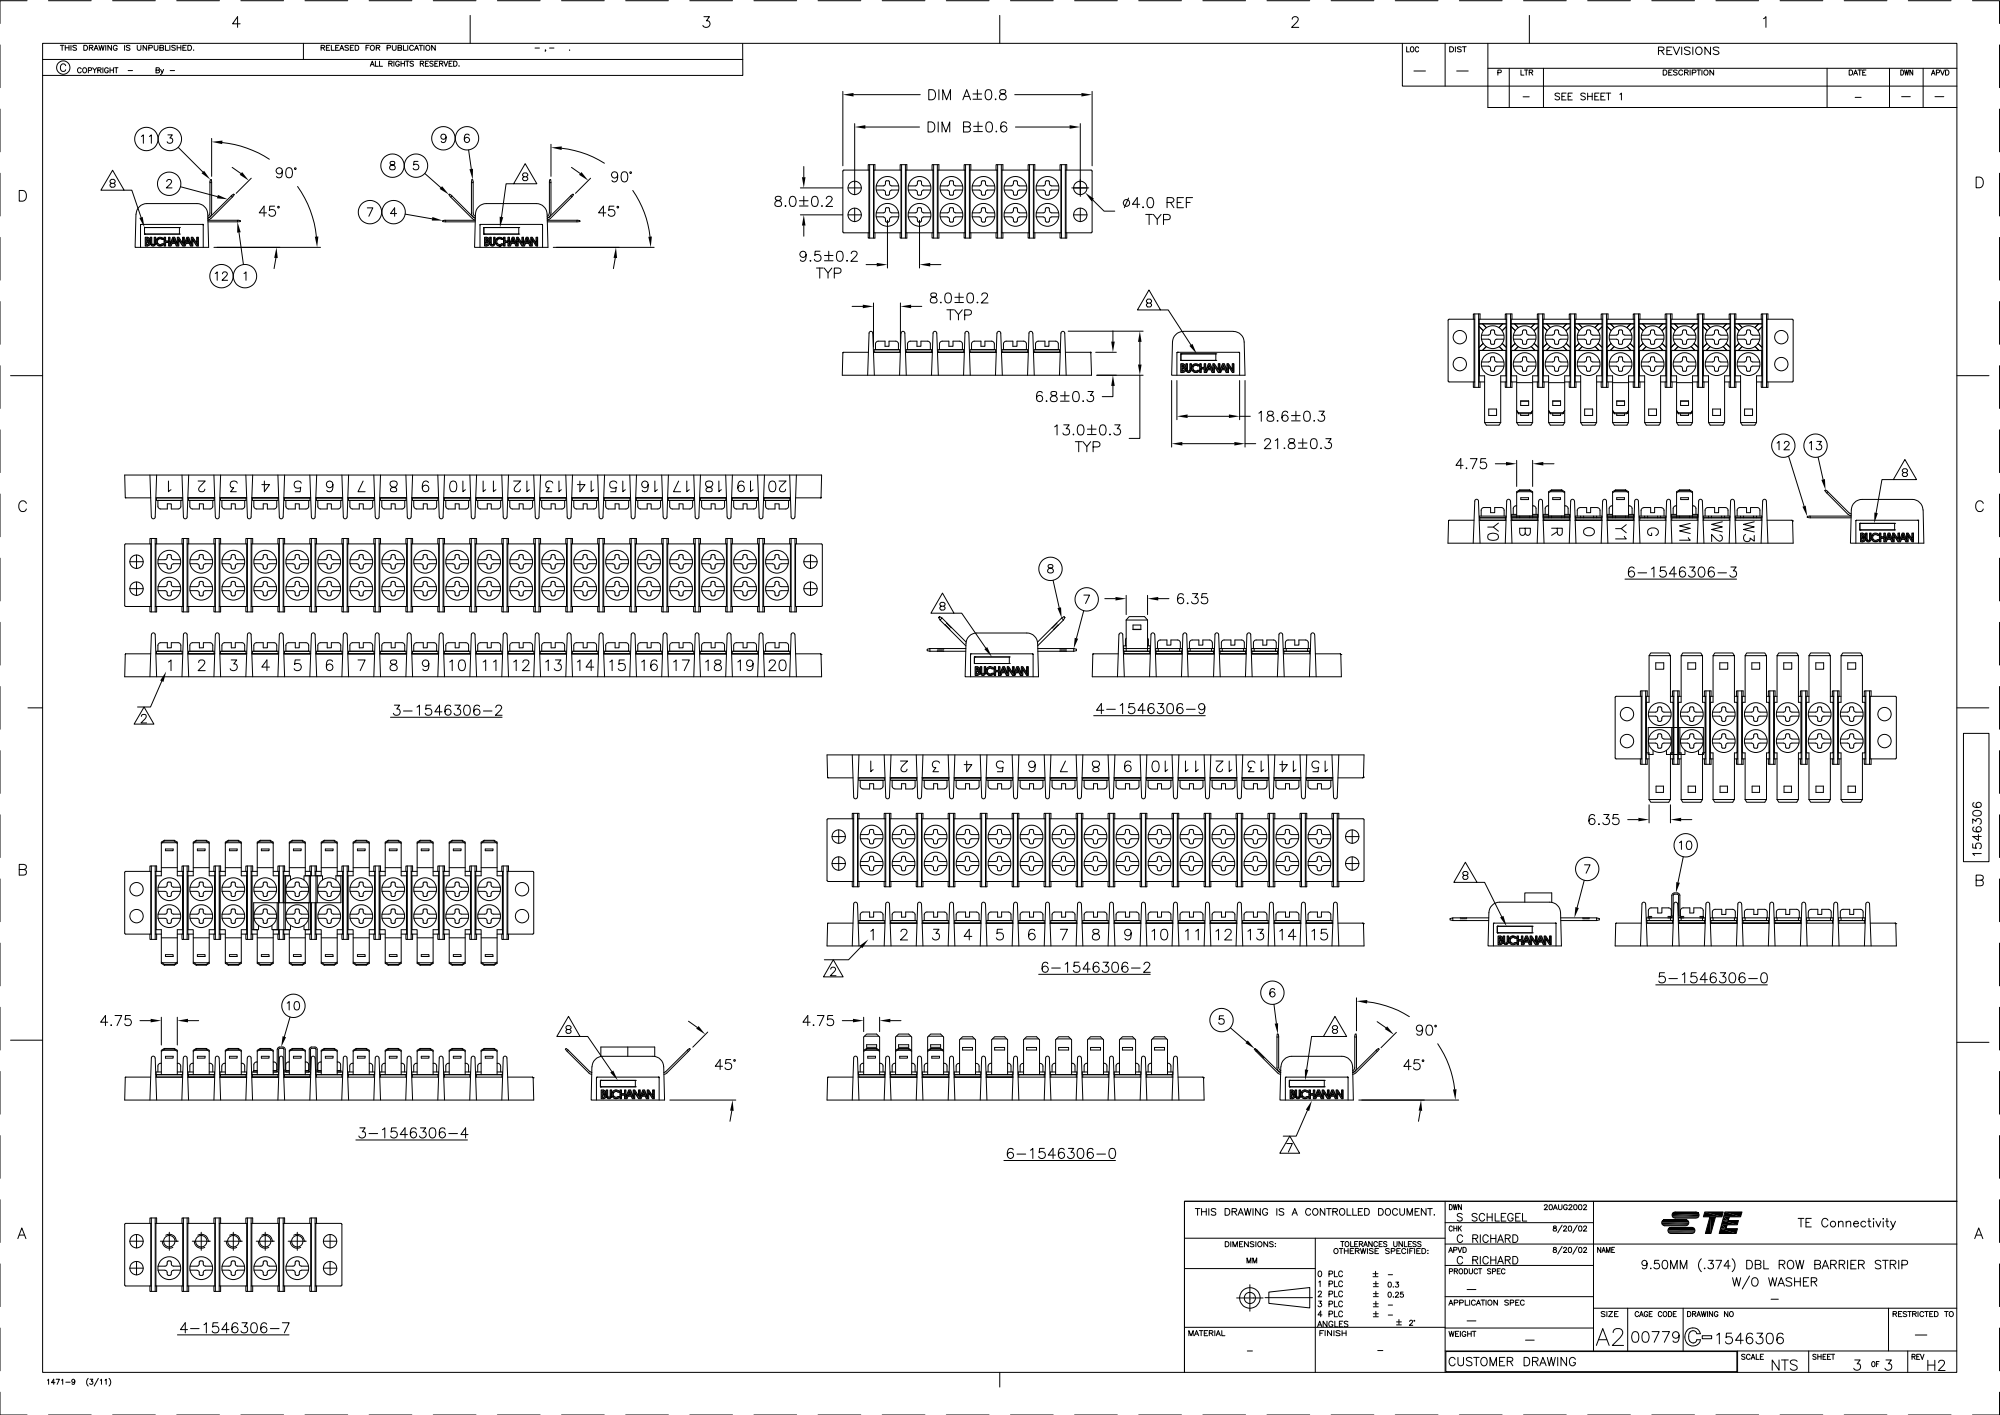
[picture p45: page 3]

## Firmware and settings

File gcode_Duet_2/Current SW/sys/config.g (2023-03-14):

; Prototype Large 3D Printer Config File
; drawing inspiration from the Jubilee config file
;!<summary>connfig.g is the file that the Duet2 fw calls after power up to learn the HW configuration of the printer and get things started. This file has loads of stuff in it. It is where we defines motors, fans, heaters, etc with a numbers and map each one to the output connector on the board where we will plug in it's cable. It defines which motors are X, Y, Z, Extruder, or Utility and defines how a single step of the motor translates into the specific motion of the nozzle, filament, or whatever the motor is hooked to.  We use it to tell teh Duet2FW that we are a core-XY style printer, the size of the bed, where our homing switches are located, how many different tools we will have, etc. Just about everything that the controller fw needs to know so it can make parts is in this file.  Loads of good stuff that we need to get right. 
;!
</summary>

;###############################################
;START OF CONTROLLER ID, DEBUG SETUP, GENERAL PREFERENCES

		;!## Set printer name
		;!Name the printer so it can identify itself. 
M550 P"ETA Large 3D Printer"                         ;! Machine name and Netbios name


		;!## Set up  Debugging and define a log file location
M111 S0        ;! Debug off
M929 P"eventlog.txt" S1                ; Start logging to file eventlog.txt


		;!## Set General Preferences
		;! call macro to create global variables we'll use later
M98 P"0:/sys/create_global_variables.g" ; added 11/29/21 by mike s
		;!Dimensions in mm, which fw to emulate, etc.
M555 P2   ;! Set to RepRapFirmware style gcode
G21       ;! Set dimensions to millimeters
G90       ;! Use absolute coordinates...
M83       ;! ...but relative extruder moves
G0 F6000  ; Set a fast speed for rapid moves. 
M575  P1 S1 B57600  ;! ENable panel Due. Comment out if we aren't using it. 

;END OF CONTROLLER ID, DEBUG SETUP, GENERALPREFERENCES
;###############################################



;###############################################
;START OF NETWORKING SETUP
		;!## Networking
		;! Set up networking parameters.
M552 S1        ;! Enable Network
M586 P0 S1     ;! Enable HTTP
M586 P1 S0	   ;! Netmask
M586 P2 S0     ;! Disable Telnet


;if network.interfaces[0].state != "active"
;  G4 S10
;  if network.interfaces[0].state != "active"
;    m552 s0
;  m291 P "Target WIFI network not found." S0
  
;END OF NETWORKING SETUP
;###############################################




;###############################################
;START OF GLOBAL VARIABLE DEFINITION
		;!## Define global variables
        ;! Global variables should now all be declatred in the create_global_variables.g file so that they can be "set" in any file without testing for their existence first.

        ;!### Z PROBE  GLOBAL VARIABLES  - X,Y offsets. Offset for the probe. 
            ;!SET two variables, global.Z_probe_Xoffset and global.Z_probe_Yoffset. 
set global.Z_probe_Xoffset =  +37.5  ;! Create variable  global.Z_probe_Xoffset and set it's value. Positive value means the probe is at a greater X value than the nozzle.
set global.Z_probe_Yoffset =  -57    ;!- Create variable  global.Z_probe_Yoffset and set it's value. Negative value means the probe is at a lower Y value than the nozzle.

;END  GLOBAL VARIABLE DEFINITION
;###############################################




;###############################################
;START OF X-Y-Z MOTION CONFIGURATION SECTION

			;!
			;!## Set up print head motion
			;!This includes the motors, how they map to the the X,Y and Z axes, plus how motor steps translate to physical motion 
			;!Before we start, clear all axis assignments so that we don't get unexpected motion.
M18 A Y Z A B C D U V W                 ; clear all axes assignments 

				;!### X-axis Motor assignment and configuration
M584 X0				;!Assign the X-axis motor to use driver0 (marked as "X" on the Duet 2 board)
M569 P0 S1      	;!Set the direction of the  driver0 (X) stepper.
M92 X160            ;!Set Steps/mm for X motor...Modified/corrected Jubilee-defined from 200 to 160 on 10/29/2020
M203 X10000			;!Set max X speed (mm/min) conservative. 16000+ possible on XY. Depends on tool and job.  Set to 10000 from 16000 due to observed out of step on 9/6/22.
M201 X1000      	;!Set max X acceleration (in mm/sec^2) for print moves.
M566 X1000			;!Set Maximum instantaneous speed change in (mm/minute). Too low and curves are super slow, too fast and there may be ringing


				;!### Y-axis Motor assignment and configuration
M584 Y1				;!Assign the Y-axis motor to use driver1 (marked as "Y" on the Duet 2 board)
;M584 Y9 			;!Assign the Y-axis motor to use driver1 (marked as "Y" on the Duet 2 board)
M569 P1 S1      	;!Set the direction of the  driver1 (Y) stepper.
M92 Y160            ;!Set Steps/mm for Y motor...Modified/corrected Jubilee-defined from 200 to 160 on 10/29/2020
M203 Y10000			;!Set max Y speed (mm/min) conservative. 16000+ possible on XY. Depends on tool and job.  Set to 10000 from 16000 due to observed out of step on 9/6/22.
M201 Y1000      	;!Set max Y acceleration (in mm/sec^2) for print moves.
M566 Y1000         ;!Set Maximum instantaneous speed change in (mm/minute). Too low and curves are super slow, too fast and there may be ringing


				;!### Z-axis Motor assignment and configuration
M584 Z6:7:8			;!Assign the Z-axis motor to use drivers 6,7,8 (marked as "E3", "E4", "E5" on the Duex Expander board)
M569 P6 S0      	;! Set the direction of the  driver6 (Front-Left Z) stepper
M569 P7 S0      	;! Set the direction of the  driver7 (Front-Right Z) stepper 
M569 P8 S0      	;! Set the direction of the  driver8 (Rear Z) stepper
M92  Z3200           ;! Set Steps/mm for Z for a T8x2 leadscrew and 0.9mm stepper. Calculation:  (16 * 400)/2
M203 Z800			;! Set max Z speed (mm/min) conservative. 
M201 Z100       	;! Set max Z acceleration (in mm/sec^2) for print moves.
M566 Z500           ;! SetMaximum instantaneous speed change in (mm/minute). Too low and movement may be jerky if mesh bed compensation is used (we do use it).


;END OF X-Y-Z MOTION CONFIGURATION SECTION
;###############################################




;###############################################
;START OF ENDSTOP SETUP SECTION
M574 X1 P"xstop" S1 ;! Define an active high (S1) limit switch at the minX end (X1) connected to the xstop pin on the Duet2 board
M574 Y1 P"ystop" S1 ;! Define an active high (S1) limit switch at the minY end (Y1) connected to the ystop pin on the Duet2 board
M574 Z1 P"zstop" S1 ;! Define an active high (S1) limit switch at the MaxZ end (Z1) connected to the zstop pin on the Duet2 board

;END OF ENDSTOP SETUP SECTION
;###############################################




;###############################################
;START OF X-Y-Z SOFT LIMITS SETUP
		;!## Soft Limits
		;!gcode commands in this section define the soft limits of movement in each direction. These limits define the maximum and minimum positions allowed during normal operations. This means that the board may send the carriage to any location within these parameters with crashing into anything. This section DOES NOT specify where the coordinate system exists within the physical boundaries of the printer. That positioning is done with the last "G1 H1" commands in the homex.g, homey.g and homez.z files. Those commands connect a machine X, Y or Z coordinate to the carriage position when the limit switch (or Z-probe) is triggered.  
		
M208 X-2:350		;!Set the Min:Max X axis soft limits. Min position is value set when X endstop is triggered.
M208 Y-10:350		;!Set the Min:Max Y axis soft limits. Min position is value set when Y endstop is triggered.
M208 Z-4:410		;!Set the Min:Max Z axis soft limits. Max position is value set when Y endstop is triggered if using the endstop at the bottom of the travel.

;###############################################
;END OF X-Y X-Y-Z MOVEMENT LIMITS SETUP





;###############################################
;START OF X-Y KINEMATICS SECTION
				;!### X-Y Kinematics. 
				;!Define us as a CoreXY type printer. We should look at the M669 command info and decide if we need to add a matrix here to address an assumed 3:1 ratio in the Z motor. seeM669 in [Duet2 wiki](https://duet3d.dozuki.com/Wiki/Gcode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)
M669 K1         ; CoreXY mode



;END OF X-Y KINEMATICS SECTION
;###############################################
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

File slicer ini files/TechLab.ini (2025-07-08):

[vendor]
repo_id = non-prusa-fff
name = BARN TechLab
config_version = 1.0.3
#config_update_url = none
#changelog_url = none

[printer_model:TechLab Mark4]
name = BARN TechLab Mark4
variants = 0.4
technology = FFF
family = BARN
bed_model = Mark4_Bed.stl
bed_texture = Mark4_bed_artwork.png
thumbnail = thumbnail.png
default_materials = PLA @TechLab; PETG @TechLab; TPU @TechLab  ;PVA @TechLab

[print:*common*]
avoid_crossing_perimeters = 0
thick_bridges = 0
bridge_acceleration = 1000
bridge_angle = 0
bridge_flow_ratio = 1
bridge_speed = 25
brim_width = 0
brim_separation = 0.1
compatible_printers = 
compatible_printers_condition = printer_model = "TechLab Mark4"
complete_objects = 0
default_acceleration = 1000
dont_support_bridges = 0
elefant_foot_compensation = 0.2
ensure_vertical_shell_thickness = 1
external_fill_pattern = rectilinear
external_perimeters_first = 0
external_perimeter_extrusion_width = 0.45
extra_perimeters = 0
extrusion_width = 0.45
fill_angle = 45
fill_density = 15%
fill_pattern = cubic
first_layer_acceleration = 800
first_layer_extrusion_width = 0.42
first_layer_height = 0.2
first_layer_speed = 20
gap_fill_speed = 40
gcode_comments = 0
infill_every_layers = 1
infill_extruder = 1
infill_extrusion_width = 0.45
infill_first = 0
infill_only_where_needed = 0
infill_overlap = 10%
interface_shells = 0
max_print_speed = 100
max_volumetric_extrusion_rate_slope_negative = 0
max_volumetric_extrusion_rate_slope_positive = 0
max_volumetric_speed = 0
min_skirt_length = 4
notes = 
overhangs = 1
only_retract_when_crossing_perimeters = 0
ooze_prevention = 0
output_filename_format = {input_filename_base}_{layer_height}mm_{printing_filament_types}_{printer_model}_{print_time}.gcode
perimeters = 2
perimeter_extruder = 1
perimeter_extrusion_width = 0.45
post_process = 
print_settings_id = 
raft_layers = 0
raft_first_layer_density = 90%
resolution = 0
seam_position = aligned
single_extruder_multi_material_priming = 1
skirts = 1
skirt_distance = 2
skirt_height = 3
small_perimeter_speed = 25
solid_infill_below_area = 0
solid_infill_every_layers = 0
solid_infill_extruder = 1
solid_infill_extrusion_width = 0.45
spiral_vase = 0
standby_temperature_delta = -5
support_material = 0
support_material_extruder = 0
support_material_extrusion_width = 0.35
support_material_interface_extruder = 0
support_material_angle = 0
support_material_buildplate_only = 0
support_material_enforce_layers = 0
support_material_contact_distance = 0.2
raft_contact_distance = 0.2
support_material_interface_contact_loops = 0
support_material_interface_layers = 2
support_material_interface_spacing = 0.2
support_material_interface_speed = 80%
support_material_pattern = rectilinear
support_material_spacing = 2
support_material_speed = 50
support_material_synchronize_layers = 0
support_material_threshold = 50
support_material_with_sheath = 0
support_material_xy_spacing = 60%
support_material_bottom_interface_layers = 0
thin_walls = 0
top_infill_extrusion_width = 0.45
top_solid_infill_speed = 40
top_fill_pattern = monotoniclines
travel_speed = 180
travel_speed_z = 12
wipe_tower = 1
wipe_tower_bridging = 10
wipe_tower_rotation_angle = 0
wipe_tower_width = 60
wipe_tower_x = 170
wipe_tower_y = 140
xy_size_compensation = 0
top_solid_min_thickness = 0.7
bottom_solid_min_thickness = 0.5
gcode_label_objects = 1
infill_anchor = 2.5
infill_anchor_max = 12
enable_dynamic_overhang_speeds = 1
support_tree_angle_slow = 30
support_tree_branch_diameter_angle = 3
support_tree_tip_diameter = 0.8
support_tree_top_rate = 30%

[print:*0.20mm*]
inherits = *common*
bottom_solid_layers = 4
bridge_flow_ratio = 0.95
external_perimeter_speed = 40
infill_acceleration = 2000
infill_speed = 60
layer_height = 0.2
perimeter_acceleration = 800
perimeter_speed = 50
solid_infill_speed = 50
top_infill_extrusion_width = 0.4
top_solid_layers = 5

[print:*0.30mm*]  
inherits = *common*
bottom_solid_layers = 4
bridge_flow_ratio = 0.95
external_perimeter_speed = 40
infill_acceleration = 2000
infill_speed = 60
layer_height = 0.3
perimeter_acceleration = 800
perimeter_speed = 50
solid_infill_speed = 50
top_infill_extrusion_width = 0.4
top_solid_layers = 4
support_material_contact_distance = 0.3



[print:*0.10mm*]
inherits = *common*
bottom_solid_layers = 7
bridge_flow_ratio = 1
bridge_speed = 20
layer_height = 0.1
perimeter_acceleration = 600
top_solid_layers = 8
support_material_contact_distance = 0.17
raft_contact_distance = 0.15
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

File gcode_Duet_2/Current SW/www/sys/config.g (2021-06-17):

; Prototype Large 3D Printer Config File
; drawing inspiration from the Jubilee config file

; Name and Identification
M550 P"ETA Large 3D Printer"                         ; Machine name and Netbios name

; Networking
M552 S1                    		; Enable Network
M586 P0 S1                       	; Enable HTTP
M586 P1 S0	                        ; Netmask
M586 P2 S0                              ; Disable Telnet

; Debugging
M111 S0                                 ; Debug off
;M929 P"eventlog.txt" S1                ; Start logging to file eventlog.txt

; General Preferences
M555 P2                                 ; Set RepRapFirmware style output
G21                                     ; Set dimensions to millimetres
G90                                     ; Send absolute coordinates...
M83                                     ; ...but relative extruder moves

; Joints
M584 X0 Y1 Z6:7:8 E3:4:5 U2   ; Map Z to drives 6, 7, 8. Map extruders to 3 and 4. Create Toolchanger Lock axis.

M569 P0 S1                  ; Drive 0 direction | X stepper
M569 P1 S1                  ; Drive 1 direction | Y Stepper

M569 P6 S0                  ; Drive 6 direction | Front Left Z
M569 P7 S0                  ; Drive 7 direction | Front Right Z
M569 P8 S0                  ; Drive 8 direction | Back Z

M569 P2 S1                  ; Drive 2 direction | Toolchanger Actuator

M569 P3 S1 D2               ; Drive 3 direction | Extruder 0 in SpreadCycle Mode
M569 P4 S1 D2               ; Drive 4 direction | Extruder 1 in SpreadCycle Mode


; Joint Kinematics
M669 K1                                 ; CoreXY mode

; Kinematic bed ball locations. Locations are extracted from CAD model assuming:
;   350x350mm build region offset from the 370x450mm plate.
;   front left corner of build region is (0, 0).
M671 X-18:376:175 Y64:64:415 S10 ; Front Left: (-18, 64) | Front Right: (376, 64) | Back: (175, 415)


; Axis and Motor Configuration
M350 X16 Y16 Z16 E16:16 U4 I1           ; Set 16x microstepping for xyz axes & extruders, 4x for toolchanger lock. Use interpolation.
M574 X1 Y1 Z1 S1                        ; Set homing switch configuration x low-end, y low-end, z low-end, all active-high (NC)
M574 U1 S1                              ; Set homing switch configuration for toolchange lock. Both switches should be wired NC and in series.

M906 X2263 Y2263                        ; LDO XY motor currents (mA). 2263mA is 80% of 2828mA Peak Current. (2828mA Peak is 2000mA RMS)
                                        ; Do not exceed 90% of full XY motor current rating without heatsinking the XY motor drivers.

M906 Z1600                              ; LDO ZZZ Motor currents (mA). Conservative.


M906 E1250                              ; Motor currents E (mA)

M906 U670 I60                           ; LDO Toolchanger Elastic Lock motor current (mA) and idle motor percentage.

                                        ; Note: Idle current setting is common across all motors (XYZZZU).

M201 X1000 Y1000                        ; XY Acceleration. Conservative. 1500+ possible.
M201 Z100                               ; LDO ZZZ Acceleration

M201 E1300:1300                         ; E Acceleration
M201 U800                               ; LDO U Accelerations (mm/s^2) conservative

M203 X13000 Y13000 Z800 E8000:8000 U9000 ; Maximum speeds (mm/min) conservative. 18000+ possible on XY. Depends on tool.
M566 X1000 Y1000 Z500 E3000 U50          ; Maximum jerk speeds mm/minute

M92 X160 Y160                           ; Steps/mm for X,Y...Modified/corrected Jubilee-defined from 200 to 160 on 10/29/2020

M92 U30.578                             ; Steps/deg for U from (200 * 4 * 13.76)/360
M92 Z3200                               ; Steps/mm for Z for a T8x2 leadscrew and 0.9mm stepper. (16 * 400)/2

;M92 E830:830                            ; Extruder - 0.9 deg/step!! This is double..commented out this step and added below M92 
M92 E420:420				 ; Extruder: This works for our L3D Dual Drive Extruder with 17HS4023 Usongshine Stepper Motor

; Set axis software limits and min/max switch-triggering positions.
; Adjusted such that (0,0) lies at the lower left corner of a 350x350mm square on the 370mmx470mm build plate.
M208 X0 Y0 Z0 S1
M208 X350 Y400 Z415.1 S0
M208 U0:200                                 ; Set Elastic Lock (U axis) max rotation angle

; Thermistors
;M305 P0 S"Bed" T10000 B3435 H0               ; BOM-specified Adjusted Terminal Lug Thermistor values. (Not for L3D)
;M305 P0 S"Bed" T10000 B3984 H0 L160          ; BOM-specified Terminal Lug Thermistor values. (Not for L3D)
M305 P0 S"Bed" T100000 B3950		      ; Built-in HT100K Bed Thermistor for H0 Bed Heater.


; PT100 Hotend Temperature Sensors. These require an external Breakout Board. For other configs, see the wiki:
; https://jubilee3d.com/index.php?title=Bondtech_Direct_Drive_Extruder 
;M305 P1 X200                                ; Map Extruder 0 sensor to PT100 Channel 0 No, not for L3D Commented out
;M305 P2 X201                                ; Map Extruder 1 sensor to PT100 Channel 1 No, not for L3D Commented out
M305 P1 S"E0 Temp" T100000 B3950	     ;HT-NTC100K Thermistor Sensor for E0 Heater on L3D
;M305 P2 S"E1 Temp" T100000 B3950	     ;HT-NTC100K Thermistor Sensor for E1 Heater on L3D

;Heaters
M950 H0 C"Bed" T0			    ;Create Bed heater and map to sensor 0....added for L3D
M950 H1 F0 C"E0 Heat" T1		    ;Create E0 heater and map Sensor 1 For L3D
;M950 H2 F1 C"E1 Heat" T2		    ;Create E1 heater and map Sensor 2 For L3D Don't have E1 right now   
M570 S30                                    ; Print will be terminated if a heater fault is not reset within 30 minutes.
M140 H0					    ;Map Heated bed to Heater H0...added for L3D
M143 H0 S100                                ; Maximum H0 (Bed) heater temperature
M143 H1 S260                                ; Maximum H1 (Extruder) heater temperature
;M143 H2 S260			            ; Maximum H2 (Extruder) heater temperature Uncomment after second extruder (H2) install
; Default heater model
;M307 H0 A270.7 C90.4 D6.7 B0 S1.0           ; Default Bed Heater Parameters, before tuning / if config-override.g is missing
M304 P25 I0.400 D66.3			    ;TEST
;M307 H0 A552.2 C281.5 D5.6 B0 S1.0          ;Testing bed heater for L3D


; Tool definitions
M563 P0 S"Extruder 0" D0 H1 F0          ; Define tool 0
;G10 P0 X-48 Y37,5 Z-2.51                 ; Set tool 0 offset from the bed (Update for bed plate thickness at 0.76 mm to 1.65 mm) Old value was Z=-0.9, which included 0.1mm foil
G10 P0 X-56 Y32 Z-0.61			; Set tool 0 offset from Z probe with tactical bed plate installed on prototype MDF bed
G10 P0 S190 R170                        ; Set tool 0 operating and standby temperatures(-273 = "off")
M572 D0 S0.1				; Set pressure advance on Extruder Drive 0

M563 P1 S"Extruder 1" D1 H2 F2          ; Define tool 1
G10 P1 X-4.23 Y45.60 Z-2.51             ; Set tool 1 offset from the bed with tool-0 as a reference.
G10 P1 S190 R170                        ; Set tool 1 operating and standby temperatures(-273 = "off")
M572 D1 S0.1                            ; Set pressure advance on Extruder Drive 1

; Fans
M106 P0 T45 S1.0 H1			; Turn on P0 H1 (E0) HotEnd fan to 100% at 45 degs... Added for L3D
M106 P2 T45 S1.0 H1			; Turn on P2 H1 (E0) Part fan to 100% at 45 degs,,, Added for L3D
;M106 P1 T45 S1.0 H2			; Turn on P1 H2 (E1) HotEnd fan to 100% at 45 degs,,, Added for L3D, commented out until tool E1 is installed
;M106 P0 S1                               ; Turn off fan 0 Commented out and replaced by above
;M106 P1 S0                               ; Turn off fan 1 Commented out and replaced by above

;Mesh Bed Leveling Settings:
M557 X20:280 Y50:350 S40		;Temporary for prototype Z probe mech Limit switch install on tool carrier.  Update when nozzle is installed

; Z probing settings
M558 P5 H3 A1 T10000 S0.02
;M558 P0
; P5 --> probe type: switch
; C2 --> endstop number
; H3 --> dive height
; A1 --> max number of times to probe
; T100000 --> travel speed between probe points
; S0.02 --> tolerance when probing multiple times

M593 F33.33  ; Reduce resonances at 33Hz based on XY vibration pattern on prints. This value could use a second opinion.

M98 P"config-user.g"                    ; Load custom user config

M501                                    ; Load saved parameters from non-volatile memory

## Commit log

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2019-11-29 Updated spreadhseet. Cleaned it up - one highlighted row per item needed, multiple rows below it for source options. Still few more to add.
    [Mark4_BOM.xlsx]
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2019-12-04 Added more materials (I think we are at 90+ % of materials now). Also cleaned up some formatting.
    [Mark4_BOM.xls]
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2019-12-07 Added readme and also a rough model of the E3D tool changer, built from their github parts.
    [E3D tool changer v8.f3z]
2019-12-07 Updated one part, replaced another with a proper version.
    [E3D tool changer v8.f3d, E3D tool changer v8.f3z, Mark3_final_printer_bridge v2.f3d]
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2019-12-11 Updated Y axis linear rails to be 500mm and cleaned up the supplier list for this and the X axis rail also.
    [Mark4_BOM.xls]
2019-12-12 Lots of changes. - New BOM - Restructured the Fusion Model directory - Added new Fusion Mark4 assembly
    [Dual Bondtech extruder with mosquito v2.f3d, Dual Bondtech extruder with mosquito v2.f3z, E3D tool changer v8.f3d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]
2019-12-12 Update README.md
    Fixed image insert
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2019-12-20 Added aliexpress mosquito clone and switched to reflect buying that. Reduced BOM cost by $200.
    [Mark4_BOM.xls]
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2020-01-08 Added additional sources of supply. Significant - added midwest steel for mic6 plates for a saving of nearly $100.
    [Mark4_BOM.xls]
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2020-01-30 New BOM file, new Fusion assembly file, new readme.md (and it's images)for the Fusion file.
    [Detailed BOM.xlsx, Mark4_BOM.xls]
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2020-02-10 Added new fusion modes, readme, and costed BOM. Also major cleanup of old files.
    [2020 v1.f3d, 4080 v1.f3d, Detailed BOM.xlsx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]
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2020-02-11 Switched flatheat M12's for M8 cap screw (+ washer) to reflect helicoil in posts. Also switched SSR selection and added thermal material for SSR heatsink.
    [Detailed BOM.xlsx]
2020-02-12 Added power folder and Ralph's power analysis, plus his explanation paper on stepper motor power. Also minor changes to BOM.
    [Detailed BOM.xlsx, Power Estimate Rev B.xlsx]
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2020-02-20 Updated BOM file with pivot tables to show parts on hand, parts we need, parts on order, etc. (Go Pivot tables!)
    [Detailed BOM.xlsx]
2020-02-20 Fixed typo on some wires
    [Detailed BOM.xlsx]
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2020-02-29 New fusion model, picture and readme. New folder and file for Duet2, Updated BOM file.
    [Detailed BOM.xlsx]
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2020-03-09 Updated BOM file to show plates, hot end, and duet extender board on order.
    [Detailed BOM.xlsx]
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2021-06-20 Added tons of readme.md and other md files autoextracted from the gcode files. Updated gcode files so they would provide autogenerated md files. Updated the python script to autogenerate the files so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
    [BARN_m117_print_a_message.g, bed.g, config.g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]
2021-06-21 Updated gcode files to better describe the macros used during the tool change process.
    [config-override.g, tfree0.g, tfree1.g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]
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2021-08-25 Modified config.g to allow two z probe types and added files fr deploying and retracting the BLTouch probe.
    [config.g, deployprobe.g, homez.g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]
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2021-11-03 Added duet fw for updating, and also updated a bunch of the gcode files
    [Query_Z.g, config.g, homey.g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]
2021-11-04 Moved soft limits to their own section in config.g. Added some more sw items to the todo list.
    [config.g]
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2021-11-09 fixed probe deploy scripts. edited limits on mesh probe locations.
    [config.g, deployprobe.g, retractprobe.g]
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2021-11-17 set config.g to use touch probe. also made a couple other tweaks. Updated homez.g to pause for user AK only if probe type is not "touch"
    [config.g, homez.g]
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2021-11-30 Added do_nothing print job for testing.; Added macro for global variable creation; created start.g to gather data for logging and level bed for printing; updated stop.g to collect and echo print stat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
    [bed.g, config.g, create_global_variables.g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]
2021-11-30 Added a G0 F6000 command to config.g to set a speed for rapid moves.
    [config.g]
2021-11-30 In config.g, changed min X to -2 to adjust for a move of the X limit switch. This allows the carriage to be in X=0 without sitting on the switch in the trigger position. ; In homex.g, added a command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
    [homex.g]
2021-11-30 start.g - added S0 option to G29 command so the height map will be use;config.g - tweaked offets values; stop.g - corrected carriage rest position at end of print. X and Y were swapped.
    [config.g, start.g, stop.g]
2021-12-14 corrected error in start.g, adjusted z offset for tool 1 in congif.g
    [config.g, start.g]
2021-12-18 Corrected error in config.g where the G31 (set z probe offsets) command was omitted. After adding it, corrected the M557 (mesh points definition) to reflect that the offsets are not longer 0. Also co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
    [bed.g, config.g]
2021-12-21 updating files to attempt to use G31 properly. Still some bugs.
    [bed.g, config.g, homey.g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]
2022-03-08 bed.g and config.g copied from Mark4 at BARN to capture changes made in December
    [bed.g, config.g]
2022-03-15 fixed a bunch of stuff
    [bed.g, config.g, create_global_variables.g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]
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2022-03-19 changed homex.g, homey.g, homez.g, and homeall.g so that the bed only drops one time. also deleted homedelta.g and homedelta.md because we are not a delta printer.
    [create_global_variables.g, homeall.g, homedelta.g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]
2022-03-19 config.g - increased max speeds from 13000mm/min to 60000mm/min. ALso changed probe speed from 30mm/min to 120mm/min. bed.g - cleaned up this file
    [bed.g, config.g]
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2022-03-22 Fixed error max Z speed command typo was resetting max X. Now fixed
    [config.g]
2022-03-22 changed number of probe points in mesh comp to 100 from 25 M557 X40:345 Y5:285 P10
    [config.g]
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2022-03-29 config.g -Moved tool temperature setting line to be after tool is defined.
    [config.g]
2022-03-29 config.g - added G29 S1 P"heightmap.csv" so that an existing heightmap will be loaded at power on and mesh bed compensation will be turned on.
    [config.g]
2022-03-29 clear_logfile.g - changed name of file in macro to match the name of our log file.
    [clear_logfile.g]
2022-04-05 config.g - Removed G29 S1 command that loaded the heightmap because loading it before z is homed makes it ineffective.
    homez.g - Added G29 S1 command to load the existing heightmap after z is homed
    [config.g, homez.g]
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2022-04-25 reworked filament load and unload so they can be run from the paneldue easily.
    [config.g, extruder_0_load_filament.g, extruder_0_unload_filament.g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]
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
